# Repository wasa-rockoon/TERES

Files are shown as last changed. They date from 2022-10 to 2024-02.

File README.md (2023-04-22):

# Tiny & Extendable Rocket Electronics Stack

モデルロケットに搭載可能な，小型かつ拡張可能な電装

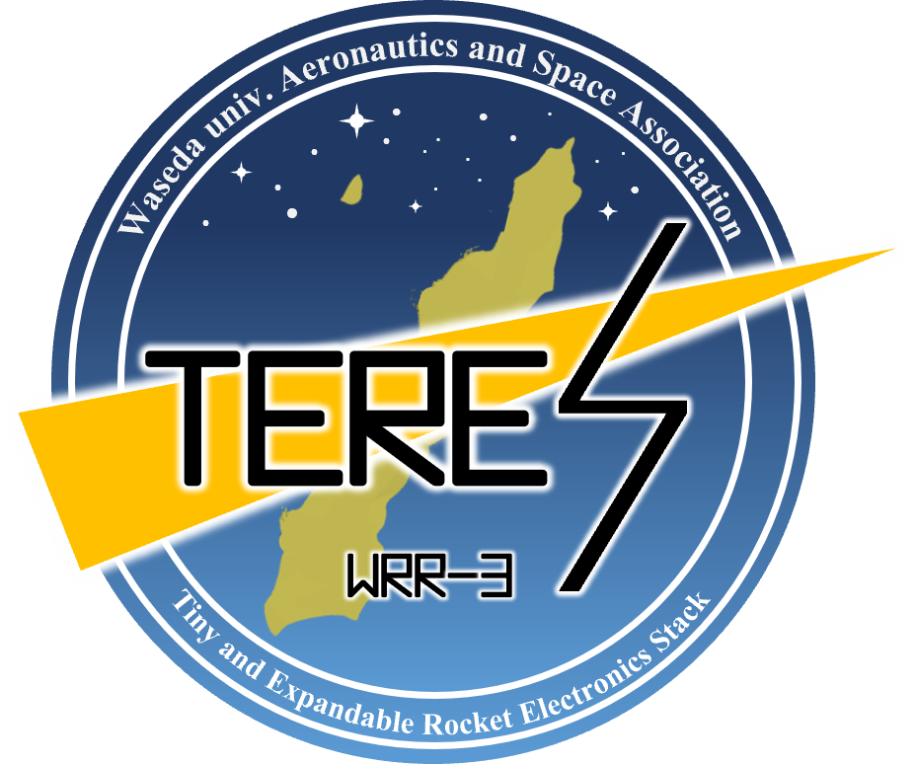
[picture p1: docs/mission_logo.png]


[テレメトリ・コマンド運用](https://wasa-rockoon.github.io/TERES/)

# 要求

- 内径40mmのボディに収まること
- 水密を確保できること
- ミッションや開発状況に応じて組み替え・拡張可能であること

# 仕様

- モジュール式
- マイコン：主にRP2040

## 外形

各モジュールは円盤状で，これを積み重ねて固定した上でロケットのボディ部またはノーズ部に搭載できる．

- 基板外径：36mm
- 基板間コネクタ：2.54mmピッチ ピンヘッダ・ピンソケット
- 固定：M2プラスチックスペーサーx4

## バス

上下のモジュールとUARTで通信し，デイジーチェーンで全体にわたるバスを形成する．

1. GND
2. UART TX
3. V+ (3.6V ~ 6V)
4. UART RX
5. GND

[通信プロトコル](https://github.com/wasa-rockoon/WCCP)

## モジュール

### LiPo電源

- 電源スイッチ
- 外部電源入力
- LiPo充電コントローラ
- LiPo温度センサ
- LiPoヒータ
- ハイサイド電流センサ

### GNSS

- GNSS受信モジュール
- バックアップ用充電池

### センサー

- 9軸センサ
- 気圧センサ
- 外部温度センサ

### テレメトリ

- TWELITE (2.4GHz)
- LoRaモジュール (920MHz)

### ロガー

- MicroSDカード
- Flash
- RTC
- バックアップ用充電池

### カメラ

- ESP32
- カメラモジュール
- マイク

## 詳細設定

### テレメトリ項目・サンプリングコード

1. ダウンリンク(10 Hz)
- GNSS
- LiPo電池残量・温度
- 気圧データ
- 9軸センサの値(姿勢を可視化するプログラムを作れたら)

2. SDカード
- 外部温度センサ(10 Hz)
- 9軸センサの値(姿勢を可視化するプログラムを作れなかったら)(10 Hz)
- カメラ映像
- マイク

### 動作モード

1. 待機フェーズ(重力加速度のみ)
2. 上昇フェーズ(垂直方向加速度>0になってから規定時間 or 気圧低下中)
3. 下降フェーズ(発射から規定時間経過後 or 気圧上昇中)
- パラシュート展開成功(垂直方向加速度==0)
- 弾道落下(ABS(垂直方向加速度)==10)
4. 着陸後フェーズ(気圧変動なし & ABS(加速度ベクトル)==10)

# ビルド

## Arduino

Arduino のライブラリディレクトリに，`software/Library/`のシンボリックリンク（またはコピー）を追加する．

# 使い方
## 動画を生成する
```
python script/make_movie.py "<連番画像フォルダのパス>"
```

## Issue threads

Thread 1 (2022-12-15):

回路設計・基板設計

fujiy, 2022-12-15:
回路設計（配線）

- [x] communication
- [x] gnss
- [x] sensor

基板設計

- [x] communication
- [x] gnss
- [x] logger
- [x] sensor

fujiy, 2022-12-15:
@KeisukeSuganuma
LoRaモジュールとの通信はI2CじゃなくてUARTかな

KeisukeSuganuma, 2022-12-15:
すみません、データシートの読み込みが甘かったです。修正後、GNSSの不足分を足したものと同時にコミットします。

Closed 2023-02-04.

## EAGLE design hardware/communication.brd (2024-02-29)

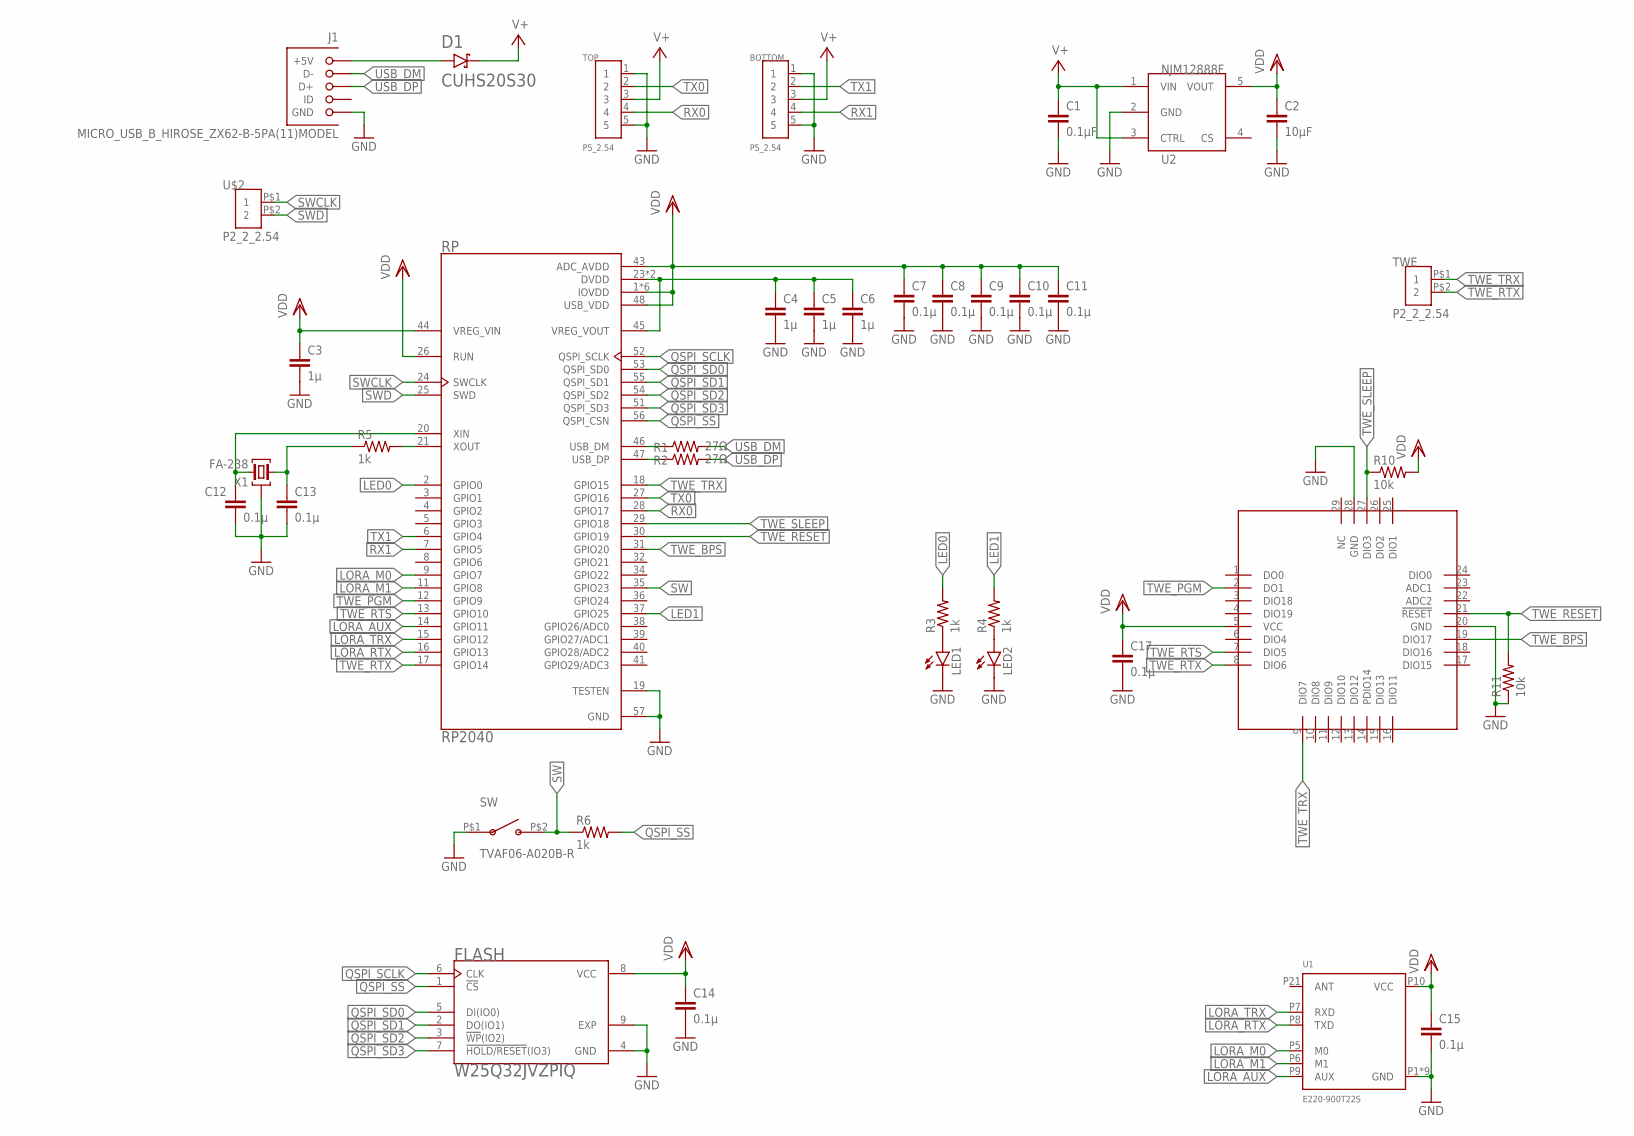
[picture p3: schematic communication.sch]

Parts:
BOTTOM: P5_2.54
C1: 0.1µF; C0402
C2: 10µF; C0402
C3, C4: 1µ; C0402
C5, C6: 1μ; C0402
C7, C8, C9, C10, C11, C15, C17: 0.1µ; C0402
C12, C13, C14: 0.1μ; C0402
D1: CUHS20S30
FLASH: W25Q32JVZPIQ; SON127P600X500X80-9N
J1: MICRO_USB_B_HIROSE_ZX62-B-5PA(11)MODEL; GHI-CONNECTORS_10118192-0001LF(MICRO-USB-B-AMPHENOL-FCI)
LED1, LED2: LEDCHIPLED_0603; CHIPLED_0603
R1, R2: 27Ω; R0402
R3, R4, R5, R6: 1k; R0402
R10, R11: 10k; R0402
RP: RP2040; QFN40P700X700X90-57N
SW: TVAF06-A020B-R
TOP: P5_2.54
TWE: P2_2_2.54; P2_2.54
U1: E220-900T22S
U2: NJM12888F; SOT95P240X110-5N
U$1: LITE
U$2: P2_2_2.54; P2_2.54
X1: FA-238

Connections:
1V2: C4.1, C5.1, C6.1, RP.23 (DVDD), RP.45 (VREG_VOUT), RP.50 (DVDD)
GND: BOTTOM.1, BOTTOM.5, C1.2, C2.2, C3.2, C4.2, C5.2, C6.2, C7.2, C8.2, C9.2, C10.2, C11.2, C12.2, C13.2, C14.2, C15.2, C17.2, FLASH.4 (GND), FLASH.9 (EXP), J1.CGND1 (GND), J1.CGND2 (GND), J1.CGND3 (GND), J1.CGND4 (GND), J1.CGND5 (GND), J1.CGND6 (GND), J1.GND, LED1.C, LED2.C, R11.1, RP.19 (TESTEN), RP.57 (GND), SW.P$1 (A), TOP.1, TOP.5, U1.P1 (GND), U1.P2 (GND), U1.P3 (GND), U1.P4 (GND), U1.P11 (GND), U1.P13 (GND), U1.P19 (GND), U1.P20 (GND), U1.P22 (GND), U2.2 (GND), U$1.20 (GND), U$1.28 (GND), X1.2 (G), X1.4 (G)
LED0: R3.2, RP.2 (GPIO0)
LED1: R4.2, RP.37 (GPIO25)
LORA_AUX: RP.14 (GPIO11), U1.P9 (AUX)
LORA_M0: RP.9 (GPIO7), U1.P5 (M0)
LORA_M1: RP.11 (GPIO8), U1.P6 (M1)
LORA_RTX: RP.16 (GPIO13), U1.P8 (TXD)
LORA_TRX: RP.15 (GPIO12), U1.P7 (RXD)
unnamed: D1.A, J1.VBUS (+5V)
unnamed: LED1.A, R3.1
unnamed: LED2.A, R4.1
unnamed: C13.1, R5.1, X1.1
QSPI_SCLK: FLASH.6 (CLK), RP.52 (QSPI_SCLK)
QSPI_SD0: FLASH.5 (DI(IO0)), RP.53 (QSPI_SD0)
QSPI_SD1: FLASH.2 (DO(IO1)), RP.55 (QSPI_SD1)
QSPI_SD2: FLASH.3 (!WP!(IO2)), RP.54 (QSPI_SD2)
QSPI_SD3: FLASH.7 (!HOLD/RESET!(IO3)), RP.51 (QSPI_SD3)
QSPI_SS: FLASH.1 (!CS), R6.2, RP.56 (QSPI_CSN)
RX0: RP.28 (GPIO17), TOP.4
RX1: BOTTOM.4, RP.7 (GPIO5)
SW: R6.1, RP.35 (GPIO23), SW.P$2 (B)
SWCLK: RP.24 (SWCLK), U$2.P$1 (1)
SWD: RP.25 (SWD), U$2.P$2 (2)
TWE_BPS: RP.31 (GPIO20), U$1.19 (DIO17)
TWE_PGM: RP.12 (GPIO9), U$1.2 (DO1)
TWE_RESET: R11.2, RP.30 (GPIO19), U$1.21 (!RESET!)
TWE_RTS: RP.13 (GPIO10), U$1.7 (DIO5)
TWE_RTX: RP.17 (GPIO14), TWE.P$2 (2), U$1.8 (DIO6)
TWE_SLEEP: R10.1, RP.29 (GPIO18), U$1.27 (DIO3)
TWE_TRX: RP.18 (GPIO15), TWE.P$1 (1), U$1.9 (DIO7)
TX0: RP.27 (GPIO16), TOP.2
TX1: BOTTOM.2, RP.6 (GPIO4)
USB_DM: J1.D-, R1.2
USB_DM_1: R1.1, RP.46 (USB_DM)
USB_DP: J1.D+, R2.2
USB_DP_1: R2.1, RP.47 (USB_DP)
V+: BOTTOM.3, C1.1, D1.C, TOP.3, U2.1 (VIN), U2.3 (CTRL)
VDD: C2.1, C3.1, C7.1, C8.1, C9.1, C10.1, C11.1, C14.1, C15.1, C17.1, FLASH.8 (VCC), R10.2, RP.1 (IOVDD), RP.10 (IOVDD), RP.22 (IOVDD), RP.26 (RUN), RP.33 (IOVDD), RP.42 (IOVDD), RP.43 (ADC_AVDD), RP.44 (VREG_VIN), RP.48 (USB_VDD), RP.49 (IOVDD), U1.P10 (VCC), U2.5 (VOUT), U$1.5 (VCC)
XIN1: C12.1, RP.20 (XIN), X1.3 (2)
XOUT1: R5.2, RP.21 (XOUT)

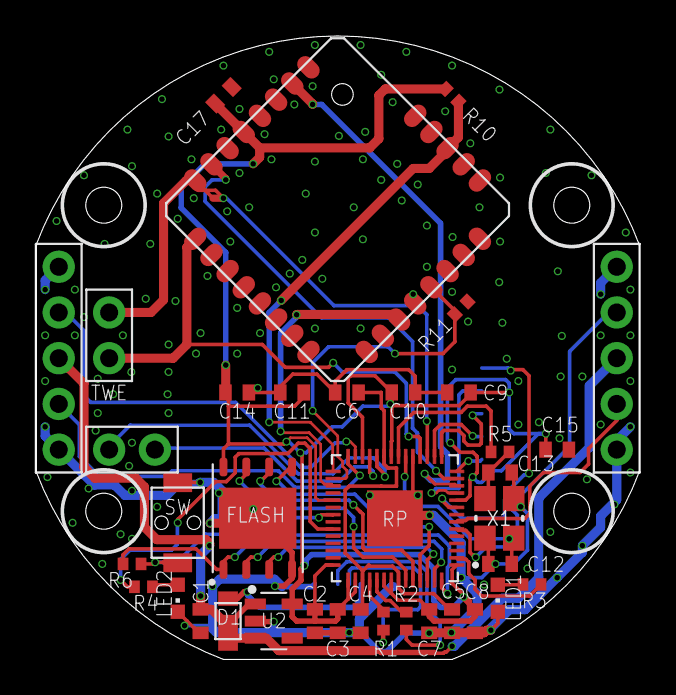
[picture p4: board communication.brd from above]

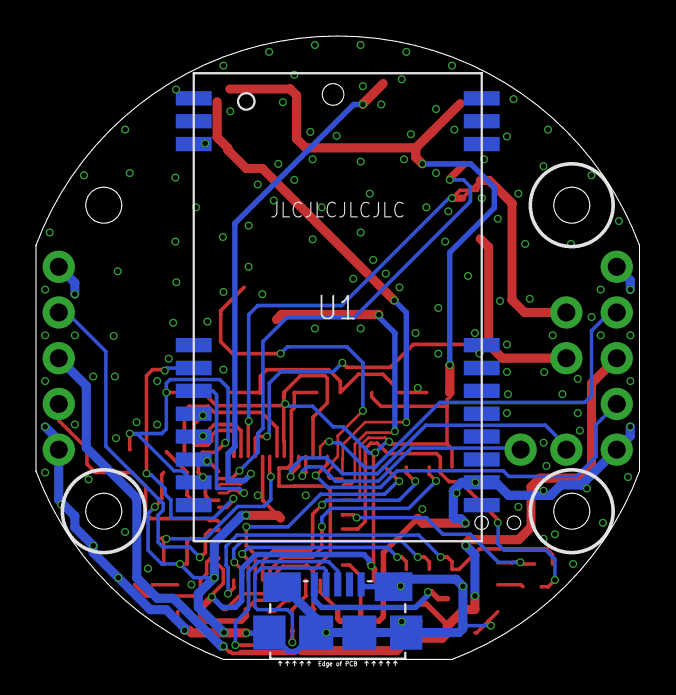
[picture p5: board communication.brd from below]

Board: 2 copper layers, 33.5 x 34.6 mm, 39 parts (2 on the bottom side), 41 nets.

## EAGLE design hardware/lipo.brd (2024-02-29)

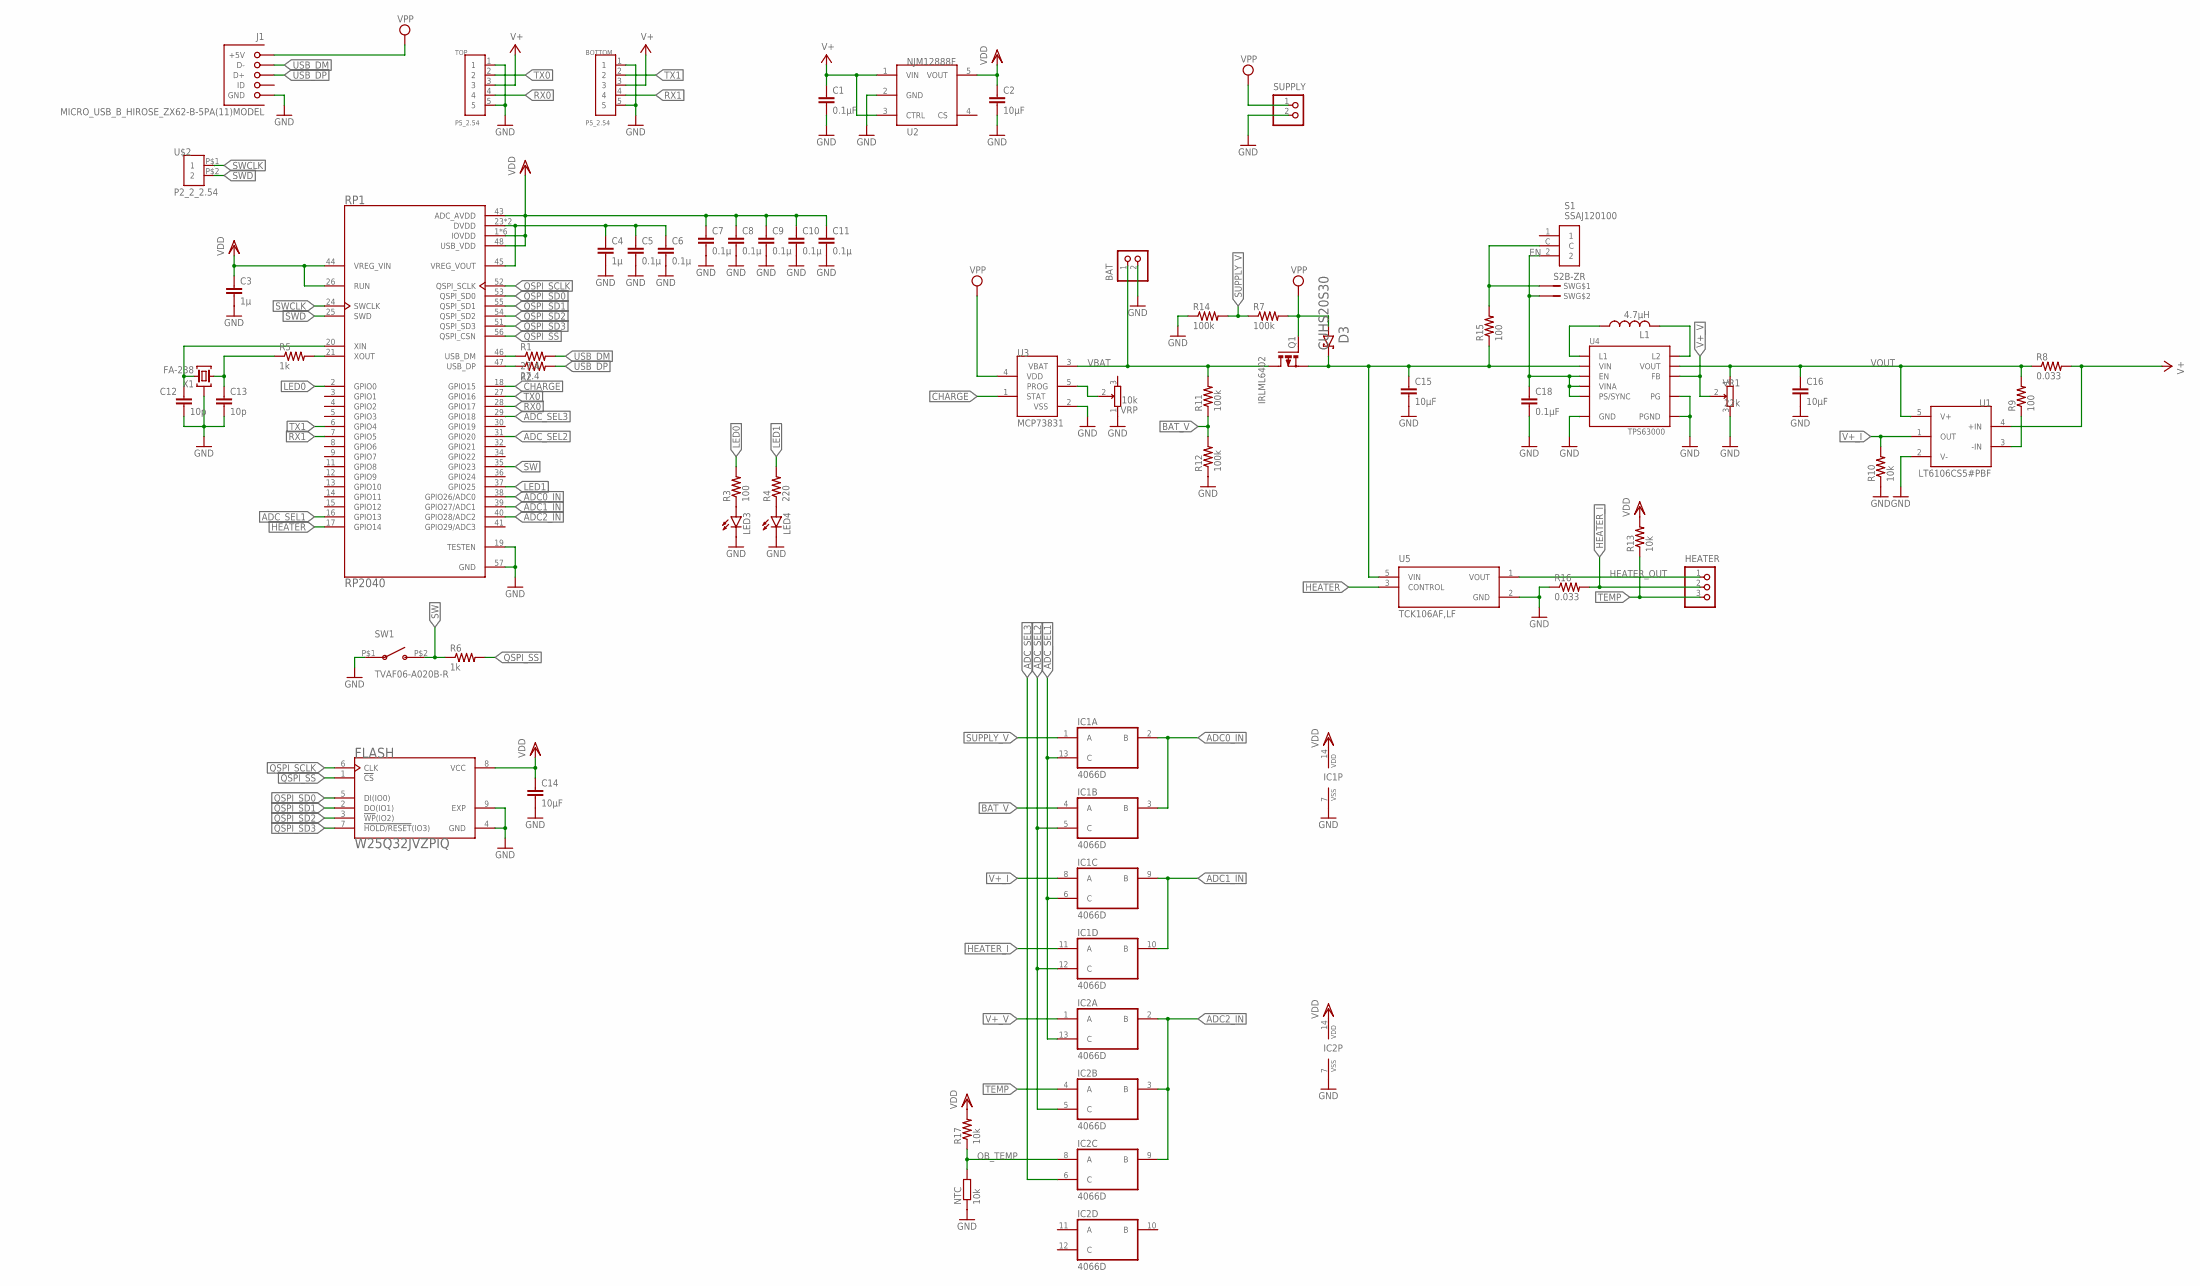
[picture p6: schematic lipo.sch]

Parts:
BAT: S2B-PH-K-S
BOTTOM: P5_2.54
C1, C18: 0.1µF; C0402
C2, C14, C15, C16: 10µF; C0402
C3, C4: 1µ; C0402
C5, C6, C7, C8, C9, C10, C11: 0.1µ; C0402
C12, C13: 10p; C0402
D3: CUHS20S30
FLASH: W25Q32JVZPIQ; SON127P600X500X80-9N
HEATER: S3B-PH-K-S
IC1, IC2: 4066D; SO14
J1: MICRO_USB_B_HIROSE_ZX62-B-5PA(11)MODEL; GHI-CONNECTORS_10118192-0001LF(MICRO-USB-B-AMPHENOL-FCI)
L1: 4.7µH; L3225M
LED3, LED4: LEDCHIPLED_0603; CHIPLED_0603
NTC: 10k; R0603
Q1: IRLML6402; SOT-23
R1, R2: 27.4; R0402
R3, R9, R15: 100; R0402
R4: 220; R0402
R5, R6: 1k; R0402
R7, R11, R12, R14: 100k; R0402
R8, R16: 0.033; R0603
R10, R13, R17: 10k; R0402
RP1: RP2040; QFN40P700X700X90-57N
S1: SSAJ120100
SUPPLY: S2B-PH-K-S
SW: S2B-ZR
SW1: TVAF06-A020B-R
TOP: P5_2.54
U1: LT6106CS5#PBF; SOT95P280X100-5N_LT6106CS5#PBF
U2: NJM12888F; SOT95P240X110-5N
U3: MCP73831; SOT23-5L
U4: TPS63000; 10-VFDFN
U5: TCK106AF,LF; IC_TCK106AF,LF
U$2: P2_2_2.54; P2_2.54
VR1: 22k; PVZ3A
VRP: 10k; PVZ3A
X1: FA-238

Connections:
1V2: C4.1, C5.1, C6.1, RP1.23 (DVDD), RP1.45 (VREG_VOUT), RP1.50 (DVDD)
ADC0_IN: IC1.2 (B), IC1.3 (B), RP1.38 (GPIO26/ADC0)
ADC1_IN: IC1.9 (B), IC1.10 (B), RP1.39 (GPIO27/ADC1)
ADC2_IN: IC2.2 (B), IC2.3 (B), IC2.9 (B), RP1.40 (GPIO28/ADC2)
ADC_SEL1: IC1.6 (C), IC1.13 (C), IC2.13 (C), RP1.16 (GPIO13)
ADC_SEL2: IC1.5 (C), IC1.12 (C), IC2.5 (C), RP1.31 (GPIO20)
ADC_SEL3: IC2.6 (C), RP1.29 (GPIO18)
BAT_V: IC1.4 (A), R11.1, R12.2
CHARGE: RP1.18 (GPIO15), U3.1 (STAT)
EN: C18.1, S1.2, SW.2, U4.6 (EN), U4.7 (PS/SYNC), U4.8 (VINA)
GND: BAT.2, BOTTOM.1, BOTTOM.5, C1.2, C2.2, C3.2, C4.2, C5.2, C6.2, C7.2, C8.2, C9.2, C10.2, C11.2, C12.2, C13.2, C14.2, C15.2, C16.2, C18.2, FLASH.4 (GND), FLASH.9 (EXP), IC1.7 (VSS), IC2.7 (VSS), J1.CGND1 (GND), J1.CGND2 (GND), J1.CGND3 (GND), J1.CGND4 (GND), J1.CGND5 (GND), J1.CGND6 (GND), J1.GND, LED3.C, LED4.C, NTC.1, R10.1, R12.1, R14.1, R16.1, RP1.19 (TESTEN), RP1.57 (GND), SUPPLY.2, SW1.P$1 (A), TOP.1, TOP.5, U1.2 (V-), U2.2 (GND), U3.2 (VSS), U4.3 (PGND), U4.9 (GND), U4.P$1 (PG), U4.P$2 (PG), U4.P$3 (PG), U4.P$4 (PG), U4.P$5 (PG), U5.2 (GND), VR1.3, VRP.1, X1.2 (G), X1.4 (G)
HEATER: RP1.17 (GPIO14), U5.3 (CONTROL)
HEATER_I: HEATER.2, IC1.11 (A), R16.2
HEATER_OUT: HEATER.1, U5.1 (VOUT)
LED0: R3.2, RP1.2 (GPIO0)
LED1: R4.2, RP1.37 (GPIO25)
unnamed: L1.1, U4.4 (L1)
unnamed: R9.1, U1.3 (-IN)
unnamed: U3.5 (PROG), VRP.2
unnamed: L1.2, U4.2 (L2)
unnamed: LED3.A, R3.1
unnamed: LED4.A, R4.1
unnamed: C13.1, R5.1, X1.1
unnamed: R15.2, S1.C, SW.1
OB_TEMP: IC2.8 (A), NTC.2, R17.1
QSPI_SCLK: FLASH.6 (CLK), RP1.52 (QSPI_SCLK)
QSPI_SD0: FLASH.5 (DI(IO0)), RP1.53 (QSPI_SD0)
QSPI_SD1: FLASH.2 (DO(IO1)), RP1.55 (QSPI_SD1)
QSPI_SD2: FLASH.3 (!WP!(IO2)), RP1.54 (QSPI_SD2)
QSPI_SD3: FLASH.7 (!HOLD/RESET!(IO3)), RP1.51 (QSPI_SD3)
QSPI_SS: FLASH.1 (!CS), R6.2, RP1.56 (QSPI_CSN)
RX0: RP1.28 (GPIO17), TOP.4
RX1: BOTTOM.4, RP1.7 (GPIO5)
SUPPLY_V: IC1.1 (A), R7.1, R14.2
SW: R6.1, RP1.35 (GPIO23), SW1.P$2 (B)
SWCLK: RP1.24 (SWCLK), U$2.P$1 (1)
SWD: RP1.25 (SWD), U$2.P$2 (2)
TEMP: HEATER.3, IC2.4 (A), R13.1
TX0: RP1.27 (GPIO16), TOP.2
TX1: BOTTOM.2, RP1.6 (GPIO4)
USB_DM: J1.D-, R1.2
USB_DM_1: R1.1, RP1.46 (USB_DM)
USB_DP: J1.D+, R2.2
USB_DP_1: R2.1, RP1.47 (USB_DP)
V+: BOTTOM.3, C1.1, R8.2, TOP.3, U1.4 (+IN), U2.1 (VIN), U2.3 (CTRL)
V+_I: IC1.8 (A), R10.2, U1.1 (OUT)
V+_V: IC2.1 (A), U4.10 (FB), VR1.2
VBAT: BAT.1, Q1.P3 (D), R11.2, U3.3 (VBAT)
VBAT_: C15.1, D3.C, Q1.P2 (S), R15.1, U4.5 (VIN), U5.5 (VIN)
VDD: C2.1, C3.1, C7.1, C8.1, C9.1, C10.1, C11.1, C14.1, FLASH.8 (VCC), IC1.14 (VDD), IC2.14 (VDD), R13.2, R17.2, RP1.1 (IOVDD), RP1.10 (IOVDD), RP1.22 (IOVDD), RP1.26 (RUN), RP1.33 (IOVDD), RP1.42 (IOVDD), RP1.43 (ADC_AVDD), RP1.44 (VREG_VIN), RP1.48 (USB_VDD), RP1.49 (IOVDD), U2.5 (VOUT)
VOUT: C16.1, R8.1, R9.2, U1.5 (V+), U4.1 (VOUT), VR1.1
VPP: D3.A, J1.VBUS (+5V), Q1.P1 (G), R7.2, SUPPLY.1, U3.4 (VDD)
XIN1: C12.1, RP1.20 (XIN), X1.3 (2)
XOUT1: R5.2, RP1.21 (XOUT)

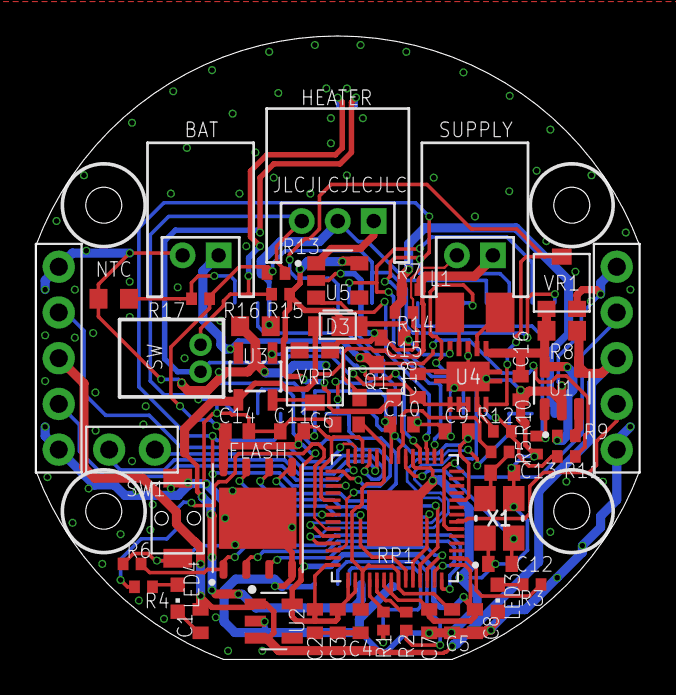
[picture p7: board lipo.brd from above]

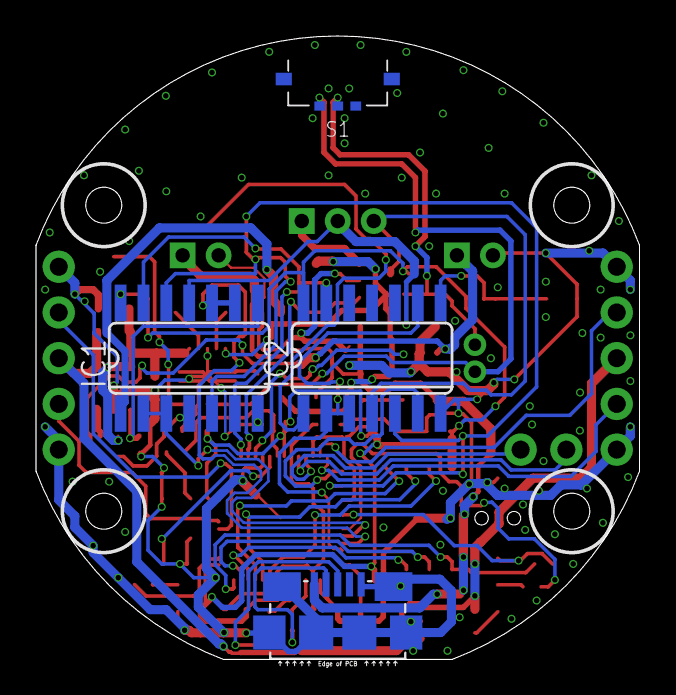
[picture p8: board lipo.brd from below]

Board: 2 copper layers, 33.5 x 34.6 mm, 62 parts (4 on the bottom side), 54 nets.

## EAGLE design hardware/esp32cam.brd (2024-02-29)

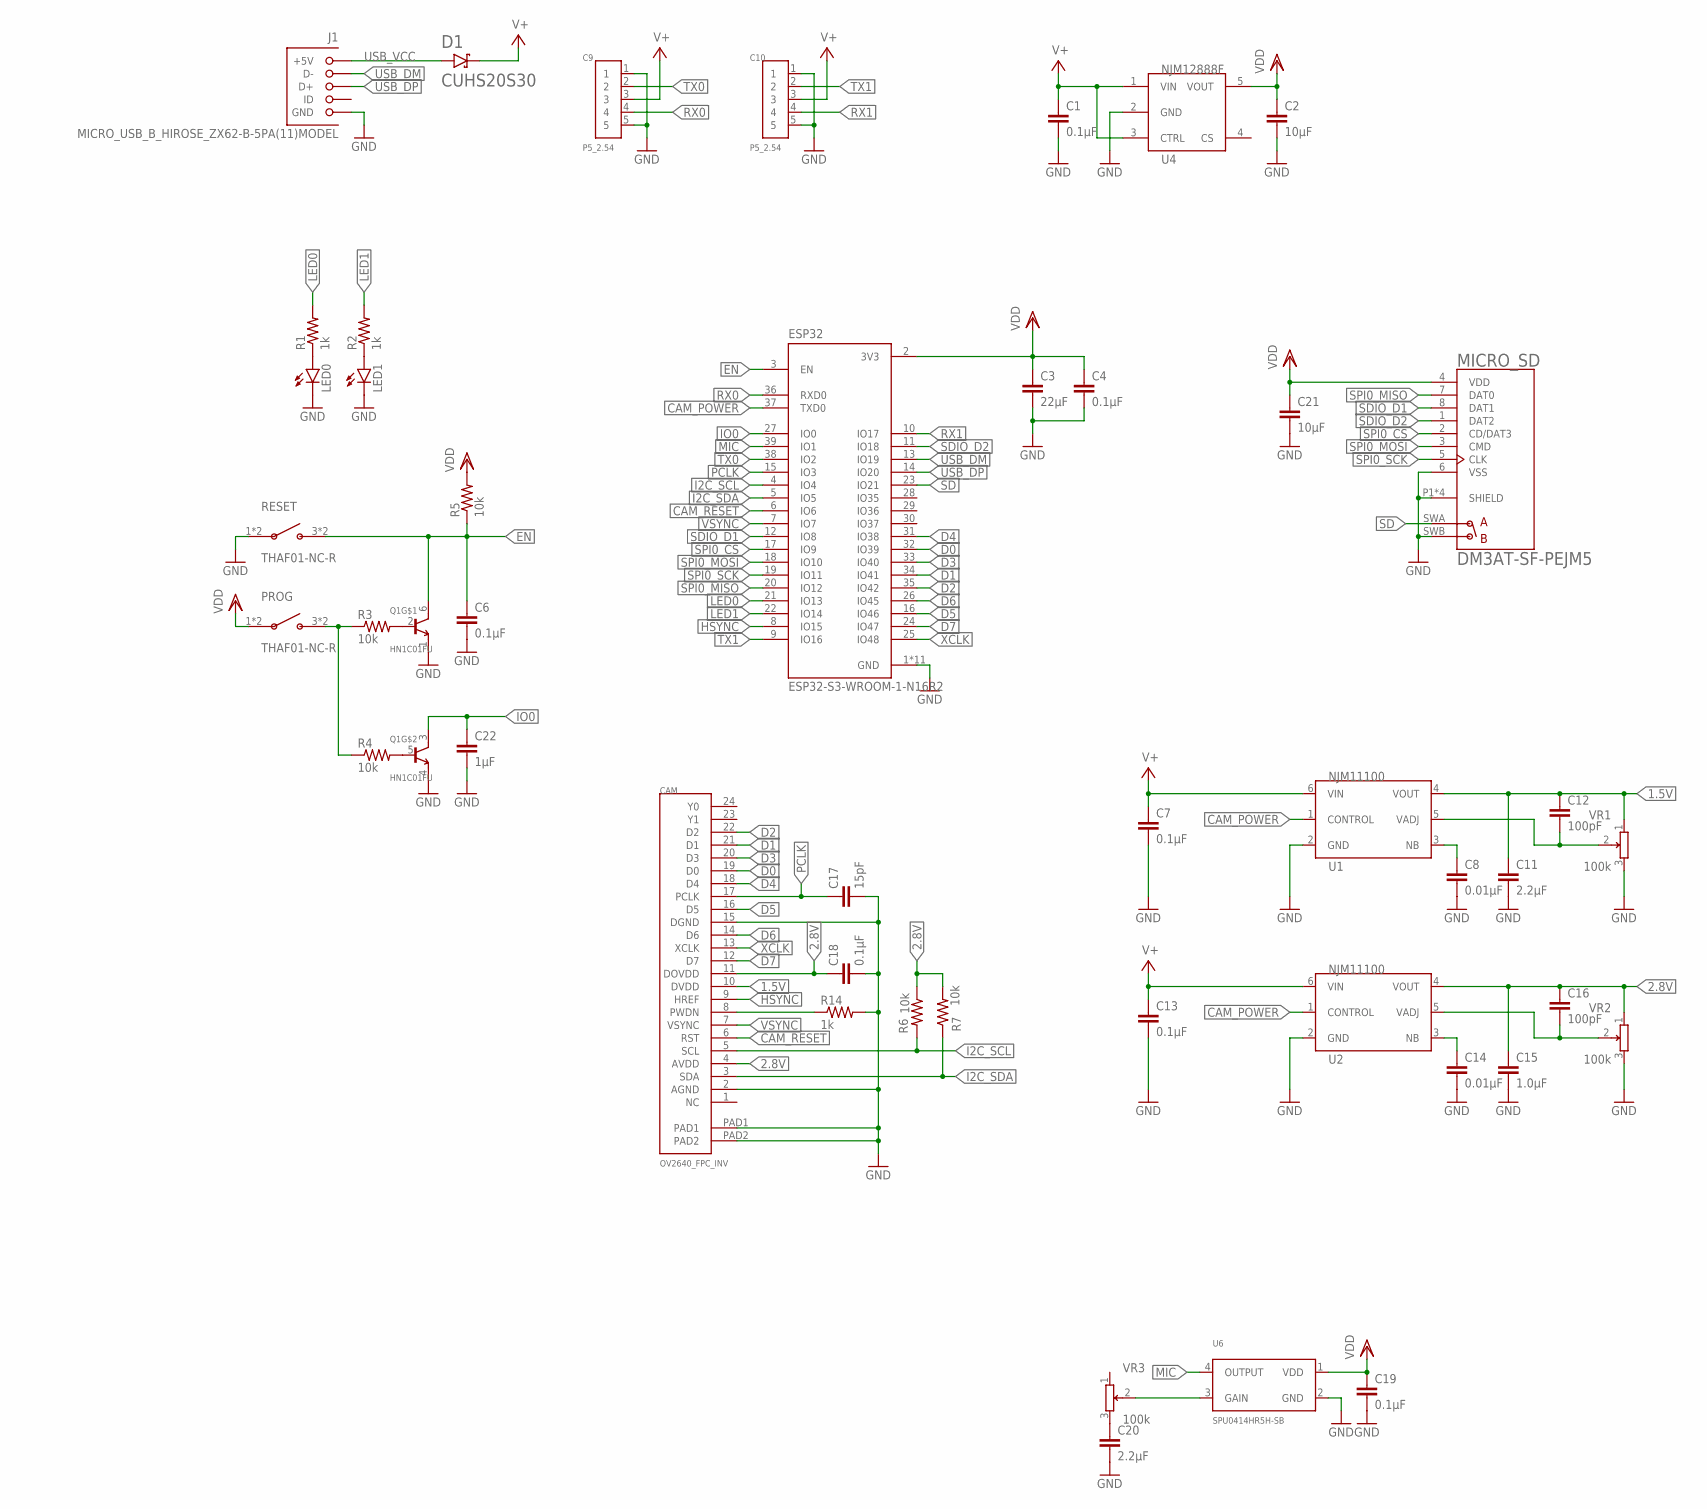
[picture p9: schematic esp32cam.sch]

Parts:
C1, C4, C6, C7, C13, C18, C19: 0.1µF; C0402
C2, C21: 10µF; C0402
C3: 22µF; C0402
C8, C14: 0.01µF; C0402
C9, C10: P5_2.54
C11, C20: 2.2µF; C0402
C12, C16: 100pF; C0402
C15: 1.0µF; C0402
C17: 15pF; C0402
C22: 1µF; C0402
CAM: OV2640_FPC_INV; FH12-24S-0.5SH
D1: CUHS20S30
ESP32: ESP32-S3-WROOM-1-N16R2; XCVR_ESP32-S3-WROOM-1-N16R2
J1: MICRO_USB_B_HIROSE_ZX62-B-5PA(11)MODEL; GHI-CONNECTORS_10118192-0001LF(MICRO-USB-B-AMPHENOL-FCI)
LED0, LED1: LEDCHIPLED_0603; CHIPLED_0603
MICRO_SD: DM3AT-SF-PEJM5; HRS_DM3AT-SF-PEJM5
PROG: THAF01-NC-R
Q1: HN1C01FU; SOT-363
R1, R2, R14: 1k; R0402
R3, R4, R5, R6, R7: 10k; R0402
RESET: THAF01-NC-R
U1, U2: NJM11100; SOT95P240X110-6N
U4: NJM12888F; SOT95P240X110-5N
U6: SPU0414HR5H-SB
VR1, VR2, VR3: 100k; PVZ3A

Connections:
1.5V: C11.1, C12.1, CAM.10 (DVDD), U1.4 (VOUT), VR1.1
2.8V: C15.1, C16.1, C18.1, CAM.4 (AVDD), CAM.11 (DOVDD), R6.1, R7.2, U2.4 (VOUT), VR2.1
CAM_POWER: ESP32.37 (TXD0), U1.1 (CONTROL), U2.1 (CONTROL)
CAM_RESET: CAM.6 (RST), ESP32.6 (IO6)
D0: CAM.19 (D0), ESP32.32 (IO39)
D1: CAM.21 (D1), ESP32.34 (IO41)
D2: CAM.22 (D2), ESP32.35 (IO42)
D3: CAM.20 (D3), ESP32.33 (IO40)
D4: CAM.18 (D4), ESP32.31 (IO38)
D5: CAM.16 (D5), ESP32.16 (IO46)
D6: CAM.14 (D6), ESP32.26 (IO45)
D7: CAM.12 (D7), ESP32.24 (IO47)
EN: C6.1, ESP32.3 (EN), Q1.6 (C), R5.1, RESET.3 (B), RESET.4 (B)
GND: C1.2, C2.2, C3.2, C4.2, C6.2, C7.2, C8.2, C9.1, C9.5, C10.1, C10.5, C11.2, C13.2, C14.2, C15.2, C17.2, C18.2, C19.2, C20.2, C21.2, C22.2, CAM.2 (AGND), CAM.15 (DGND), CAM.PAD1, CAM.PAD2, ESP32.1 (GND), ESP32.40 (GND), ESP32.41_1 (GND), ESP32.41_2 (GND), ESP32.41_3 (GND), ESP32.41_4 (GND), ESP32.41_5 (GND), ESP32.41_6 (GND), ESP32.41_7 (GND), ESP32.41_8 (GND), ESP32.41_9 (GND), J1.CGND1 (GND), J1.CGND2 (GND), J1.CGND3 (GND), J1.CGND4 (GND), J1.CGND5 (GND), J1.CGND6 (GND), J1.GND, LED0.C, LED1.C, MICRO_SD.6 (VSS), MICRO_SD.P1 (SHIELD), MICRO_SD.P2 (SHIELD), MICRO_SD.P3 (SHIELD), MICRO_SD.P4 (SHIELD), MICRO_SD.SWB (B), Q1.1 (E), Q1.4 (E), R14.2, RESET.1 (A), RESET.2 (A), U1.2 (GND), U2.2 (GND), U4.2 (GND), U6.2 (GND), VR1.3, VR2.3
HSYNC: CAM.9 (HREF), ESP32.8 (IO15)
I2C_SCL: CAM.5 (SCL), ESP32.4 (IO4), R6.2
I2C_SDA: CAM.3 (SDA), ESP32.5 (IO5), R7.1
IO0: C22.1, ESP32.27 (IO0), Q1.3 (C)
LED0: ESP32.21 (IO13), R1.2
LED1: ESP32.22 (IO14), R2.2
MIC: ESP32.39 (IO1), U6.4 (OUTPUT)
unnamed: C8.1, U1.3 (NB)
unnamed: C12.2, U1.5 (VADJ), VR1.2
unnamed: C14.1, U2.3 (NB)
unnamed: C16.2, U2.5 (VADJ), VR2.2
unnamed: PROG.3 (B), PROG.4 (B), R3.1, R4.1
unnamed: LED0.A, R1.1
unnamed: LED1.A, R2.1
unnamed: Q1.2 (B), R3.2
unnamed: CAM.8 (PWDN), R14.1
unnamed: Q1.5 (B), R4.2
unnamed: U6.3 (GAIN), VR3.2
unnamed: C20.1, VR3.3
PCLK: C17.1, CAM.17 (PCLK), ESP32.15 (IO3)
RX0: C9.4, ESP32.36 (RXD0)
RX1: C10.4, ESP32.10 (IO17)
SD: ESP32.23 (IO21), MICRO_SD.SWA (A)
SDIO_D1: ESP32.12 (IO8), MICRO_SD.8 (DAT1)
SDIO_D2: ESP32.11 (IO18), MICRO_SD.1 (DAT2)
SPI0_CS: ESP32.17 (IO9), MICRO_SD.2 (CD/DAT3)
SPI0_MISO: ESP32.20 (IO12), MICRO_SD.7 (DAT0)
SPI0_MOSI: ESP32.18 (IO10), MICRO_SD.3 (CMD)
SPI0_SCK: ESP32.19 (IO11), MICRO_SD.5 (CLK)
TX0: C9.2, ESP32.38 (IO2)
TX1: C10.2, ESP32.9 (IO16)
USB_DM: ESP32.13 (IO19), J1.D-
USB_DP: ESP32.14 (IO20), J1.D+
USB_VCC: D1.A, J1.VBUS (+5V)
V+: C1.1, C7.1, C9.3, C10.3, C13.1, D1.C, U1.6 (VIN), U2.6 (VIN), U4.1 (VIN), U4.3 (CTRL)
VDD: C2.1, C3.1, C4.1, C19.1, C21.1, ESP32.2 (3V3), MICRO_SD.4 (VDD), PROG.1 (A), PROG.2 (A), R5.2, U4.5 (VOUT), U6.1 (VDD)
VSYNC: CAM.7 (VSYNC), ESP32.7 (IO7)
XCLK: CAM.13 (XCLK), ESP32.25 (IO48)

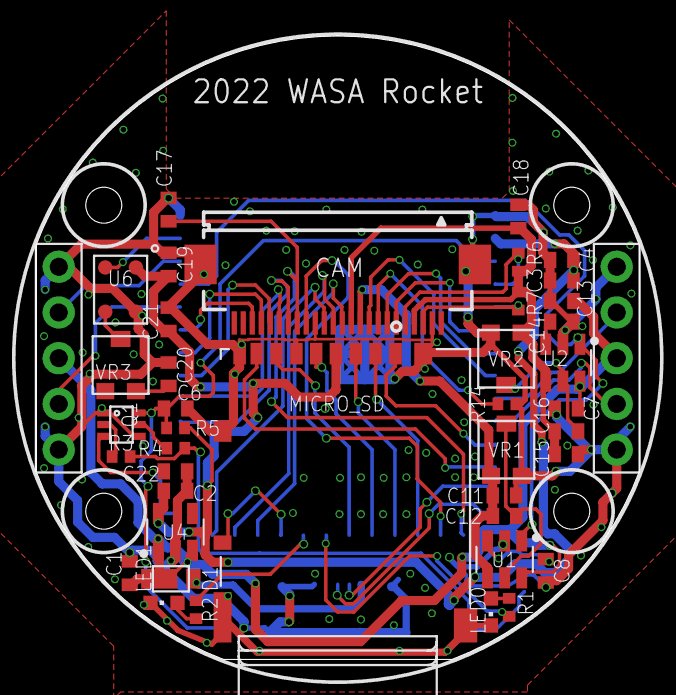
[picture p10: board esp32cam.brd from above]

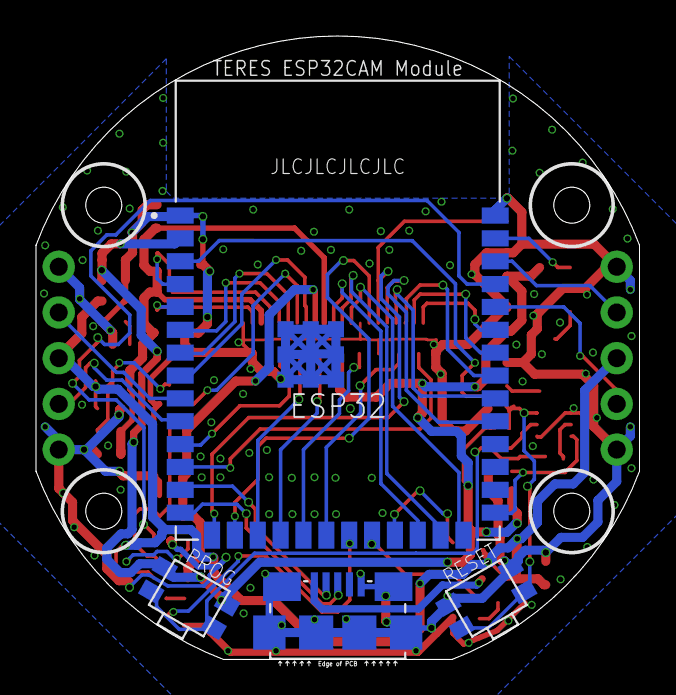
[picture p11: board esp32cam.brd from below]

Board: 2 copper layers, 33.5 x 34.6 mm, 46 parts (4 on the bottom side), 52 nets.

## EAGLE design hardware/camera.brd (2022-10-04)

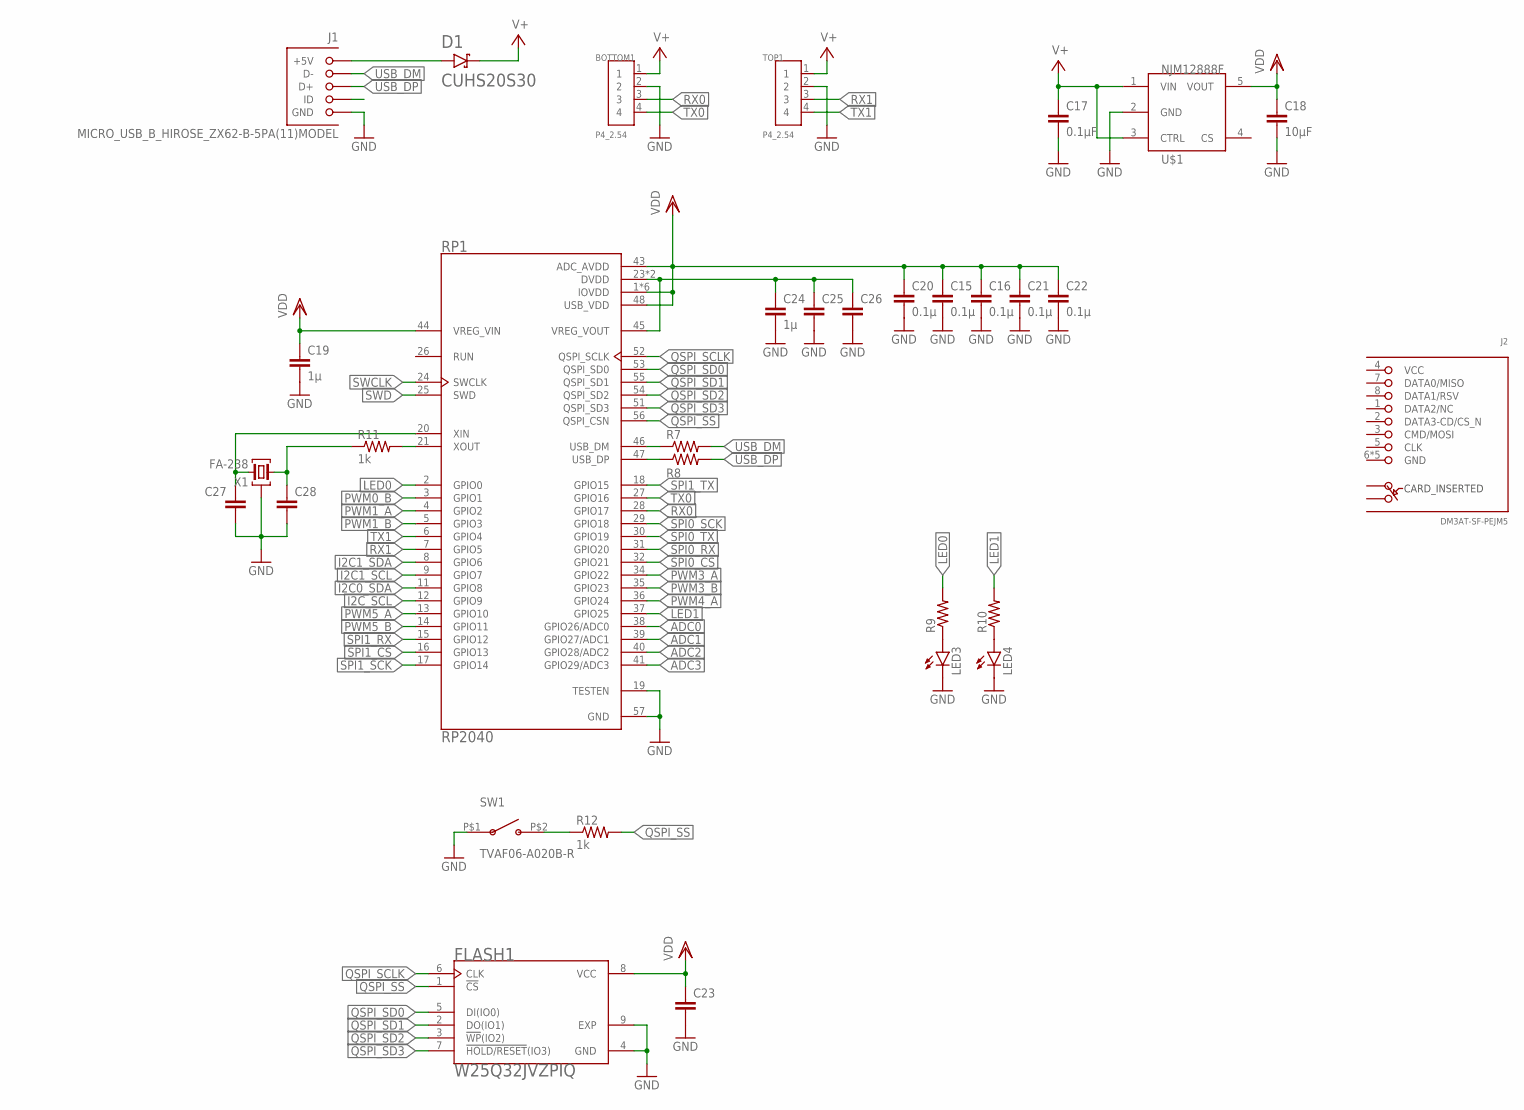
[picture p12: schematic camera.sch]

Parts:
BOTTOM1: P4_2.54
C15, C16, C20, C21, C22: 0.1µ; C0402
C17: 0.1µF; C0402
C18: 10µF; C0402
C19, C24: 1µ; C0402
C23, C25, C26, C27, C28: C-EUC0402; C0402
D1: CUHS20S30
FLASH1: W25Q32JVZPIQ; SON127P600X500X80-9N
J1: MICRO_USB_B_HIROSE_ZX62-B-5PA(11)MODEL; GHI-CONNECTORS_10118192-0001LF(MICRO-USB-B-AMPHENOL-FCI)
J2: DM3AT-SF-PEJM5
LED3, LED4: LEDCHIPLED_0603; CHIPLED_0603
R7, R8, R9, R10: R-US_R0402; R0402
R11, R12: 1k; R0402
RP1: RP2040; QFN40P700X700X90-57N
SW1: TVAF06-A020B-R
TOP1: P4_2.54
U$1: NJM12888F; SOT95P240X110-5N
X1: FA-238

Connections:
1V2: C24.1, C25.1, C26.1, RP1.23 (DVDD), RP1.45 (VREG_VOUT), RP1.50 (DVDD)
ADC0: RP1.38 (GPIO26/ADC0)
ADC1: RP1.39 (GPIO27/ADC1)
ADC2: RP1.40 (GPIO28/ADC2)
ADC3: RP1.41 (GPIO29/ADC3)
GND: BOTTOM1.2, C15.2, C16.2, C17.2, C18.2, C19.2, C20.2, C21.2, C22.2, C23.2, C24.2, C25.2, C26.2, C27.2, C28.2, FLASH1.4 (GND), FLASH1.9 (EXP), J1.CGND1 (GND), J1.CGND2 (GND), J1.CGND3 (GND), J1.CGND4 (GND), J1.CGND5 (GND), J1.CGND6 (GND), J1.GND, LED3.C, LED4.C, RP1.19 (TESTEN), RP1.57 (GND), SW1.P$1 (A), TOP1.2, U$1.2 (GND), X1.2 (G), X1.4 (G)
I2C0_SDA: RP1.11 (GPIO8)
I2C1_SCL: RP1.9 (GPIO7)
I2C1_SDA: RP1.8 (GPIO6)
I2C_SCL: RP1.12 (GPIO9)
LED0: R9.2, RP1.2 (GPIO0)
LED1: R10.2, RP1.37 (GPIO25)
unnamed: D1.A, J1.VBUS (+5V)
unnamed: LED3.A, R9.1
unnamed: LED4.A, R10.1
unnamed: C28.1, R11.1, X1.1
unnamed: R12.1, SW1.P$2 (B)
PWM0_B: RP1.3 (GPIO1)
PWM1_A: RP1.4 (GPIO2)
PWM1_B: RP1.5 (GPIO3)
PWM3_A: RP1.34 (GPIO22)
PWM3_B: RP1.35 (GPIO23)
PWM4_A: RP1.36 (GPIO24)
PWM5_A: RP1.13 (GPIO10)
PWM5_B: RP1.14 (GPIO11)
QSPI_SCLK: FLASH1.6 (CLK), RP1.52 (QSPI_SCLK)
QSPI_SD0: FLASH1.5 (DI(IO0)), RP1.53 (QSPI_SD0)
QSPI_SD1: FLASH1.2 (DO(IO1)), RP1.55 (QSPI_SD1)
QSPI_SD2: FLASH1.3 (!WP!(IO2)), RP1.54 (QSPI_SD2)
QSPI_SD3: FLASH1.7 (!HOLD/RESET!(IO3)), RP1.51 (QSPI_SD3)
QSPI_SS: FLASH1.1 (!CS), R12.2, RP1.56 (QSPI_CSN)
RX0: BOTTOM1.3, RP1.28 (GPIO17)
RX1: RP1.7 (GPIO5), TOP1.3
SPI0_CS: RP1.32 (GPIO21)
SPI0_RX: RP1.31 (GPIO20)
SPI0_SCK: RP1.29 (GPIO18)
SPI0_TX: RP1.30 (GPIO19)
SPI1_CS: RP1.16 (GPIO13)
SPI1_RX: RP1.15 (GPIO12)
SPI1_SCK: RP1.17 (GPIO14)
SPI1_TX: RP1.18 (GPIO15)
SWCLK: RP1.24 (SWCLK)
SWD: RP1.25 (SWD)
TX0: BOTTOM1.4, RP1.27 (GPIO16)
TX1: RP1.6 (GPIO4), TOP1.4
USB_DM: J1.D-, R7.2
USB_DM_1: R7.1, RP1.46 (USB_DM)
USB_DP: J1.D+, R8.2
USB_DP_1: R8.1, RP1.47 (USB_DP)
V+: BOTTOM1.1, C17.1, D1.C, TOP1.1, U$1.1 (VIN), U$1.3 (CTRL)
VDD: C15.1, C16.1, C18.1, C19.1, C20.1, C21.1, C22.1, C23.1, FLASH1.8 (VCC), RP1.1 (IOVDD), RP1.10 (IOVDD), RP1.22 (IOVDD), RP1.33 (IOVDD), RP1.42 (IOVDD), RP1.43 (ADC_AVDD), RP1.44 (VREG_VIN), RP1.48 (USB_VDD), RP1.49 (IOVDD), U$1.5 (VOUT)
XIN1: C27.1, RP1.20 (XIN), X1.3 (2)
XOUT1: R11.2, RP1.21 (XOUT)

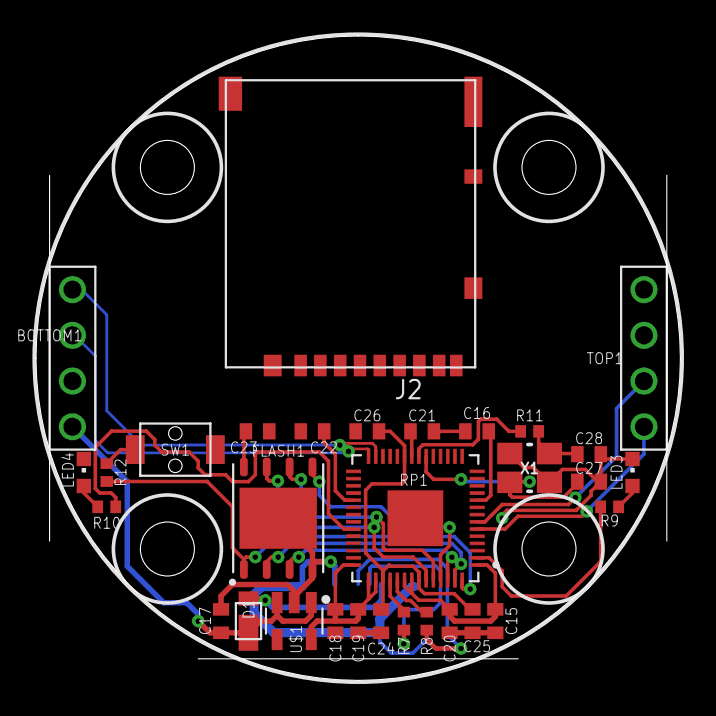
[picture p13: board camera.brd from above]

Board: 2 copper layers, 35.8 x 35.8 mm, 32 parts (1 on the bottom side), 27 nets.

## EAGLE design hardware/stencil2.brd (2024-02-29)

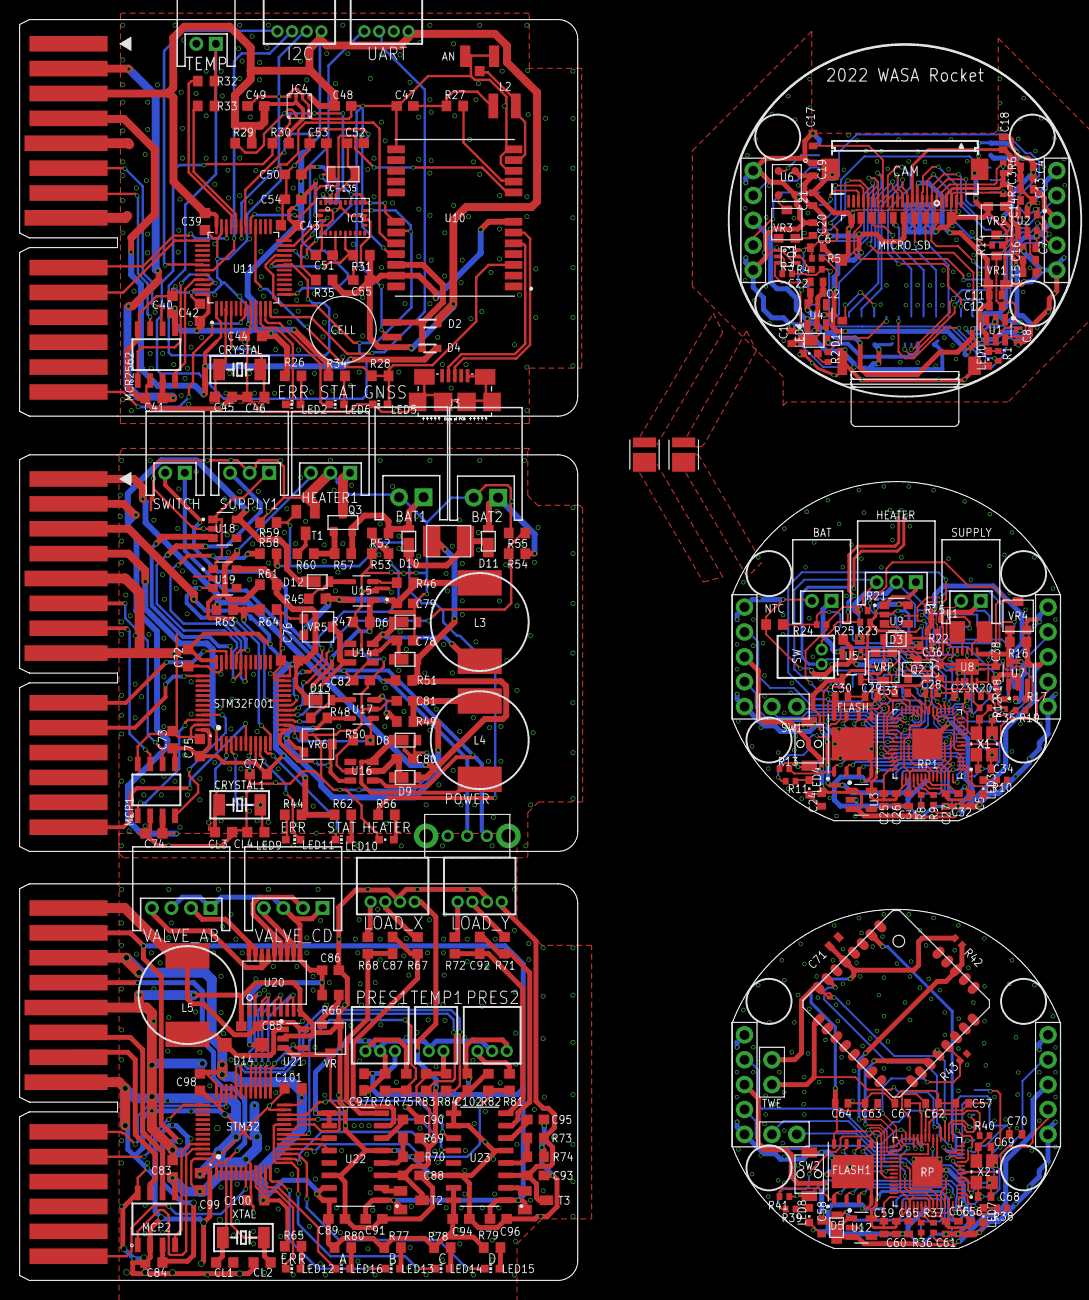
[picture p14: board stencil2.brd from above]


Board: 2 copper layers, 107.2 x 128.8 mm, 331 parts (10 on the bottom side), 303 nets.

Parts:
AB: S4B-PH-K-S
AN: U.FL-R-SMT; U.FL_SMT
BAT: S2B-PH-K-S
BAT1, BAT2: S2B-XH-A
BOTTOM, BOTTOM1: P5_2.54
C1, C4, C6, C7, C13, C18, C19, C24, C37, C58: 0.1µF; C0402
C2, C21, C25, C30, C36, C38, C59: 10µF; C0402
C3: 22µF; C0402
C5, C23, C27, C28, C29, C32, C33, C56, C57, C61, C62, C63, C70, C71: 0.1µ; C0402
C8, C14: 0.01µF; C0402
C9, C10: P5_2.54
C11, C20: 2.2µF; C0402
C12, C16: 100pF; C0402
C15: 1.0µF; C0402
C17: 15pF; C0402
C22: 1µF; C0402
C26, C31, C60, C65: 1µ; C0402
C34, C35: 10p; C0402
C39, C40, C41, C42, C43, C44, C72, C73, C74, C75, C76, C77, C83, C84, C98, C99, C100, C101: C0603K
C45, C46: 15pF; C0603K
C47: 47pF; C0603
C48, C49, C50, C51, C55: 0.1µ; C0603
C52, C53, C97, C102: C0603
C54, C82, C87, C89, C90, C92, C94, C95: 0.1µF; C0603
C64, C68, C69: 0.1μ; C0402
C66, C67: 1μ; C0402
C78, C79, C80, C81: 47µF; C0603
C85: 4.7µF; C0603
C86: 2.2µF; C0603
C88, C91, C93, C96: 10µF; C0603
CAM: OV2640_FPC_INV; FH12-24S-0.5SH
CD: S4B-PH-K-S
CELL: DCK-3R3E; DC,DCK
CL1, CL2, CL3, CL4: 15pF; C0603K
CRYSTAL, CRYSTAL1: 32.768kHz; FC-255
D1, D3, D5, D6, D7, D8, D9, D10, D11, D12, D13: CUHS20S30
D2, D4: RB521S-30TE61; SODFL1608X70N
D14: SOD123
ESP32: ESP32-S3-WROOM-1-N16R2; XCVR_ESP32-S3-WROOM-1-N16R2
FC-135: FC-135
FLASH, FLASH1: W25Q32JVZPIQ; SON127P600X500X80-9N
HEATER, HEATER1: S3B-PH-K-S
I2C: S4B-ZR
IC1, IC2: 4066D; SO14
IC3: BN055; LGA-28_3.80X5.20/0.5
IC4: BME280
J1, J2, J3, J4: MICRO_USB_B_HIROSE_ZX62-B-5PA(11)MODEL; GHI-CONNECTORS_10118192-0001LF(MICRO-USB-B-AMPHENOL-FCI)
L1: 4.7µH; L3225M
L2: 33Ω; SM-NE29
L3, L4: 22µH; NR10050
L5: 10µH; NR10050
LED0, LED1, LED3, LED4, LED7, LED8, LED10: CHIPLED_0603
LED2, LED5, LED6, LED9, LED11, LED12, LED13, LED14, LED15, LED16: CHIP-LED0603
LOAD_X: S4B-ZR
LOAD_Y: S4B-ZR
MCP1, MCP2, MCP2562: MCP2562-E/SN; SOIC127P600X175-8N
MICRO_SD: DM3AT-SF-PEJM5; HRS_DM3AT-SF-PEJM5
NTC: 10k; R0603
POWER: SK-12D01-VG4
PRES1, PRES2: S3B-ZR
PROG: THAF01-NC-R
Q1: HN1C01FU; SOT-363
Q2, Q3: IRLML6402; SOT-23
R1, R2, R12, R13, R14, R38, R39, R40, R41: 1k; R0402
R3, R4, R5, R6, R7, R18, R21, R24, R42, R43: 10k; R0402
R8, R9: 27.4; R0402
R10, R17, R23: 100; R0402
R11: 220; R0402
R15, R19, R20, R22: 100k; R0402
R16, R25, R45, R48: 0.033; R0603
R26, R28, R29, R30, R31, R34, R35: R0603
R27: 10; R0603
R32, R47, R50, R51, R57, R59, R61, R70, R74, R75, R81, R83: 10k; R0603
R33, R53, R55, R64, R84: 100k; R0603
R36, R37: 27Ω; R0402
R44, R58, R60, R62, R65, R77, R78, R79, R80: 1k; R0603
R46, R49, R67, R68, R71, R72: 100; R0603
R52, R54, R63, R66: 1M; R0603
R56: 470; R0603
R69, R73: 22k; R0603
R76, R82: 15k; R0603
RESET: THAF01-NC-R
RP, RP1: RP2040; QFN40P700X700X90-57N
S1: SSAJ120100
STM32, STM32F001: STM32F072-LQFP48; LQFP48
SUPPLY: S2B-PH-K-S
SUPPLY1: S3B-PH-K-S
SW: S2B-ZR
SW1, SW2: TVAF06-A020B-R
SWITCH: S2B-PH-K-S
T1: SOT23-EBC
T2, T3: SOT23-BEC
TEMP: S2B-PH-K-S
TEMP1: S2B-ZR
TOP, TOP1: P5_2.54
TWE: P2_2_2.54; P2_2.54
U1, U2: NJM11100; SOT95P240X110-6N
U3, U4, U12: NJM12888F; SOT95P240X110-5N
U5: MCP73831; SOT23-5L
U6: SPU0414HR5H-SB
U7, U15, U17: LT6106CS5#PBF; SOT95P280X100-5N_LT6106CS5#PBF
U8: TPS63000; 10-VFDFN
U9, U18, U19: TCK106AF,LF; IC_TCK106AF,LF
U10: NEO-M9N-00B; XCVR_NEO-M9N-00B
U11: STM32L433CCT6; QFP50P900X900X160-48N
U13: E220-900T22S
U14, U16: LT1616ES6TRMPBF; SOT-6_S
U20: TD62083AFNG; SSOP18-P-225-0.65
U21: LT1930; SOT95P240X110-5N
U22, U23: HX711; SOP127P600X180-16N
U$1, U$7, U$9: EDGE30
U$2, U$5: P2_2_2.54; P2_2.54
U$3, U$4: S1S0-3030XX9506
U$6: LITE
U$8: SMD1812P125TS; SMD1812P
UART: S4B-ZR
VR, VR1, VR2, VR3: 100k; PVZ3A
VR4, VR5, VR6: 22k; PVZ3A
VRP: 10k; PVZ3A
X1, X2: FA-238
XTAL: 32.768kHz; FC-255

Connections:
1.5V: C11.1, C12.1, CAM.10, U1.4, VR1.1
1PPS: LED5.A, R28.1, R28.2, U10.3, U11.28
1V1: C65.1, C66.1, C67.1, RP.23, RP.45, RP.50
1V2: C31.1, C32.1, C33.1, RP1.23, RP1.45, RP1.50
2.8V: C15.1, C16.1, C18.1, CAM.4, CAM.11, R6.1, R7.2, U2.4, VR2.1
3V3: C81.1, L4.2, R48.1, R49.2, U17.5, VR6.3
5V: C79.1, L3.2, R45.1, R46.2, U15.5, VR5.3
!SHDN!: C82.1, POWER.B, SWITCH.2, U14.4, U16.4
ADC0_IN: IC1.2, IC1.3, RP1.38
ADC1_IN: IC1.9, IC1.10, RP1.39
ADC2_IN: IC2.2, IC2.3, IC2.9, RP1.40
ADC_SEL1: IC1.6, IC1.13, IC2.13, RP1.16
ADC_SEL2: IC1.5, IC1.12, IC2.5, RP1.31
ADC_SEL3: IC2.6, RP1.29
ANT: AN.SIG, L2.2, U10.11
A_OUT: AB.2, U20.P17, U20.P18
BAT1: BAT1.1, D10.A, Q3.P2, R52.2, R57.2
BAT1_V: R52.1, R53.2, STM32F001.18
BAT2: BAT2.1, D11.A, R54.2
BAT2_V: R54.1, R55.2, STM32F001.17
BAT_V: IC1.4, R19.1, R20.2
BNO_!RESET!: IC3.11, R31.1, U11.20
B_OUT: AB.4, U20.P15, U20.P16
CAM_POWER: ESP32.37, U1.1, U2.1
CAM_RESET: CAM.6, ESP32.6
CANH1: MCP2562.7, U$1.7
CANH2: MCP1.7, U$7.7
CANH3: MCP2.7, U$9.7
CANL1: MCP2562.6, U$1.6
CANL2: MCP1.6, U$7.6
CANL3: MCP2.6, U$9.6
CAN_RX: MCP2562.4, U11.45
CAN_RX1: MCP1.4, STM32F001.45
CAN_RX2: MCP2.4, STM32.45
CAN_TX: MCP2562.1, U11.46
CAN_TX1: MCP1.1, STM32F001.46
CAN_TX2: MCP2.1, STM32.46
CHARGE: RP1.18, U5.1
C_OUT: CD.2, U20.P13, U20.P14
D0: CAM.19, ESP32.32
D1: CAM.21, ESP32.34
D2: CAM.22, ESP32.35
D3: CAM.20, ESP32.33
D4: CAM.18, ESP32.31
D5: CAM.16, ESP32.16
D6: CAM.14, ESP32.26
D7: CAM.12, ESP32.24
D_OUT: CD.4, U20.P11, U20.P12
EN: C6.1, ESP32.3, Q1.6, R5.1, RESET.3, RESET.4
EN1: C37.1, S1.2, SW.2, U8.6, U8.7, U8.8
GND: C1.2, C2.2, C3.2, C4.2, C6.2, C7.2, C8.2, C9.1, C9.5, C10.1, C10.5, C11.2, C13.2, C14.2, C15.2, C17.2, C18.2, C19.2, C20.2, C21.2, C22.2, CAM.2, CAM.15, CAM.PAD1, CAM.PAD2, ESP32.1, ESP32.40, ESP32.41_1, ESP32.41_2, ESP32.41_3, ESP32.41_4, ESP32.41_5, ESP32.41_6, ESP32.41_7, ESP32.41_8, ESP32.41_9, J1.CGND1, J1.CGND2, J1.CGND3, J1.CGND4, J1.CGND5, J1.CGND6, J1.GND, LED0.C, LED1.C, MICRO_SD.6, MICRO_SD.P1, MICRO_SD.P2, MICRO_SD.P3, MICRO_SD.P4, MICRO_SD.SWB, Q1.1, Q1.4, R14.2, RESET.1, RESET.2, U1.2, U2.2, U4.2, U6.2, VR1.3, VR2.3
GND1: BAT.2, BOTTOM.1, BOTTOM.5, C5.2, C23.2, C24.2, C25.2, C26.2, C27.2, C28.2, C29.2, C30.2, C31.2, C32.2, C33.2, C34.2, C35.2, C36.2, C37.2, C38.2, FLASH.4, FLASH.9, IC1.7, IC2.7, J2.CGND1, J2.CGND2, J2.CGND3, J2.CGND4, J2.CGND5, J2.CGND6, J2.GND, LED3.C, LED4.C, NTC.1, R18.1, R20.1, R22.1, R25.1, RP1.19, RP1.57, SUPPLY.2, SW1.P$1, TOP.1, TOP.5, U3.2, U5.2, U7.2, U8.3, U8.9, U8.P$1, U8.P$2, U8.P$3, U8.P$4, U8.P$5, U9.2, VR4.3, VRP.1, X1.2, X1.4
GND2: AN.GND1, AN.GND2, C39.2, C40.2, C41.2, C42.2, C43.2, C44.2, C45.1, C46.1, C47.2, C48.2, C49.2, C50.2, C51.2, C52.1, C53.1, C54.2, C55.2, CELL.-, I2C.2, IC3.2, IC3.5, IC3.6, IC3.17, IC3.18, IC3.25, IC4.1, IC4.5, IC4.7, J3.CGND1, J3.CGND2, J3.CGND3, J3.CGND4, J3.CGND5, J3.CGND6, J3.GND, LED5.C, MCP2562.2, MCP2562.8, TEMP.2, U10.10, U10.12, U10.13, U10.24, U11.8, U11.23, U11.35, U11.47, U$1.5, U$1.8, UART.2
GND3: BOTTOM1.1, BOTTOM1.5, C56.2, C57.2, C58.2, C59.2, C60.2, C61.2, C62.2, C63.2, C64.2, C65.2, C66.2, C67.2, C68.2, C69.2, C70.2, C71.2, FLASH1.4, FLASH1.9, J4.CGND1, J4.CGND2, J4.CGND3, J4.CGND4, J4.CGND5, J4.CGND6, J4.GND, LED7.C, LED8.C, R43.1, RP.19, RP.57, SW2.P$1, TOP1.1, TOP1.5, U12.2, U13.P1, U13.P2, U13.P3, U13.P4, U13.P11, U13.P13, U13.P19, U13.P20, U13.P22, U$6.20, U$6.28, X2.2, X2.4
GND4: BAT1.2, BAT2.2, C72.2, C73.2, C74.2, C75.2, C76.2, C77.2, C78.2, C79.2, C80.2, C81.2, C82.2, CL3.1, CL4.1, D6.A, D8.A, HEATER1.2, LED10.C, MCP1.2, MCP1.8, R47.1, R50.1, R53.1, R55.1, R59.1, R64.1, STM32F001.8, STM32F001.23, STM32F001.35, STM32F001.47, SUPPLY1.2, T1.E, U14.2, U15.2, U16.2, U17.2, U18.2, U19.2, U$7.5, U$7.8, VR5.1, VR6.1
GND5: C83.2, C84.2, C85.2, C86.2, C88.2, C89.2, C90.2, C91.2, C93.2, C94.2, C95.2, C96.2, C97.2, C98.2, C99.2, C100.2, C101.2, C102.2, CL1.1, CL2.1, LOAD_X.2, LOAD_Y.2, MCP2.2, MCP2.8, PRES1.2, PRES2.2, R70.1, R74.1, R76.1, R82.1, STM32.8, STM32.23, STM32.35, STM32.47, TEMP1.2, U20.P9, U21.2, U22.5, U22.9, U22.10, U22.14, U23.5, U23.9, U23.10, U23.14, U$9.5, U$9.8, VR.1
GPS_!RESET!: U10.8, U11.29
GPS_RTX: U10.20, U11.31
GPS_TRX: U10.21, U11.30
HEATER: RP1.17, U9.3
HEATER1: R58.1, STM32F001.30
HEATER+: HEATER1.1, Q3.P3
HEATER_I: HEATER.2, IC1.11, R25.2
HEATER_OUT: HEATER.1, U9.1
HSYNC: CAM.9, ESP32.8
I2C1_SCL: I2C.4, U11.42
I2C1_SDA: I2C.3, U11.43
I2C2_SCL: IC3.19, IC4.4, R30.1, U10.19, U11.21
I2C2_SDA: IC3.20, IC4.3, R29.1, U10.18, U11.22
I2C_SCL: CAM.5, ESP32.4, R6.2
I2C_SDA: CAM.3, ESP32.5, R7.1
IO0: C22.1, ESP32.27, Q1.3
LED0: ESP32.21, R1.2
LED1: ESP32.22, R2.2
LED2: R10.2, RP1.2
LED3: R11.2, RP1.37
LED4: R38.2, RP.2
LED5: R39.2, RP.37
LORA_AUX: RP.14, U13.P9
LORA_M0: RP.9, U13.P5
LORA_M1: RP.11, U13.P6
LORA_RTX: RP.16, U13.P8
LORA_TRX: RP.15, U13.P7
MIC: ESP32.39, U6.4
unnamed: C8.1, U1.3
unnamed: C12.2, U1.5, VR1.2
unnamed: C14.1, U2.3
unnamed: C16.2, U2.5, VR2.2
unnamed: PROG.3, PROG.4, R3.1, R4.1
unnamed: LED3.A, R10.1
unnamed: LED0.A, R1.1
unnamed: LED1.A, R2.1
unnamed: Q1.2, R3.2
unnamed: CAM.8, R14.1
unnamed: Q1.5, R4.2
unnamed: LED4.A, R11.1
unnamed: U6.3, VR3.2
unnamed: C20.1, VR3.3
unnamed: C35.1, R12.1, X1.1
unnamed: U5.5, VRP.2
unnamed: R17.1, U7.3
unnamed: L1.1, U8.4
unnamed: L1.2, U8.2
unnamed: R23.2, S1.C, SW.1
unnamed: U11.7, U$1.15
unnamed: R27.2, U10.9
unnamed: C47.1, L2.1, R27.1
unnamed: CELL.+, D2.1, D4.1, U10.22
unnamed: C51.1, IC3.9
unnamed: C53.2, FC-135.P$2, IC3.27
unnamed: C52.2, FC-135.P$1, IC3.26
unnamed: LED6.C, U11.11
unnamed: LED6.A, R34.2
unnamed: IC3.4, R35.1
unnamed: LED2.C, U11.10
unnamed: D5.A, J4.VBUS
unnamed: LED7.A, R38.1
unnamed: LED8.A, R39.1
unnamed: C69.1, R40.1, X2.1
unnamed: CL4.2, CRYSTAL1.1, STM32F001.4
unnamed: R46.1, U15.3
unnamed: R49.1, U17.3
unnamed: POWER.C, R51.1, SWITCH.1
unnamed: SUPPLY1.1, U18.1, U19.1
unnamed: LED10.A, R56.2
unnamed: Q3.P1, R57.1, R60.1
unnamed: R56.1, R58.2, R59.2, T1.B
unnamed: R60.2, T1.C
unnamed: LED11.C, STM32F001.11
unnamed: LED11.A, R62.2
unnamed: LED12.C, STM32.10
unnamed: LED12.A, R65.2
unnamed: D14.A, L5.2, U21.1
unnamed: R66.1, VR.3
unnamed: C87.2, R67.1, U22.7
unnamed: C87.1, R68.1, U22.8
unnamed: T2.B, U22.2
unnamed: C90.1, U22.6
unnamed: R69.1, R70.2, U22.4
unnamed: C92.2, R71.1, U23.7
unnamed: C92.1, R72.1, U23.8
unnamed: T3.B, U23.2
unnamed: C95.1, U23.6
unnamed: R73.1, R74.2, U23.4
unnamed: PRES1.3, R75.2
unnamed: LED13.C, STM32.12
unnamed: LED13.A, R77.2
unnamed: LED14.C, STM32.20
unnamed: LED14.A, R78.2
unnamed: C46.2, CRYSTAL.1, U11.4
unnamed: C45.2, CRYSTAL.2, U11.3
unnamed: CL3.2, CRYSTAL1.2, STM32F001.3
unnamed: LED9.C, STM32F001.10
unnamed: LED2.A, R26.2
unnamed: LED15.C, STM32.14
unnamed: LED9.A, R44.2
unnamed: LED15.A, R79.2
unnamed: CL2.2, STM32.4, XTAL.1
unnamed: CL1.2, STM32.3, XTAL.2
unnamed: LED16.C, STM32.11
unnamed: LED16.A, R80.2
unnamed: PRES2.3, R81.2
NRST: STM32.7, U$9.15
NRST1: STM32F001.7, U$7.15
OB_TEMP: IC2.8, NTC.2, R24.1
PCLK: C17.1, CAM.17, ESP32.15
POWER_FB: STM32.19, U21.3, VR.2
POWER_ON: STM32.25, U21.4
PRESSURE_1: R75.1, R76.2, STM32.18
PRESSURE_2: R81.1, R82.2, STM32.15
QSPI_SCLK: FLASH.6, RP1.52
QSPI_SCLK1: FLASH1.6, RP.52
QSPI_SD0: FLASH.5, RP1.53
QSPI_SD1: FLASH.2, RP1.55
QSPI_SD2: FLASH.3, RP1.54
QSPI_SD3: FLASH.7, RP1.51
QSPI_SD4: FLASH1.5, RP.53
QSPI_SD5: FLASH1.2, RP.55
QSPI_SD6: FLASH1.3, RP.54
QSPI_SD7: FLASH1.7, RP.51
QSPI_SS: FLASH.1, R13.2, RP1.56
QSPI_SS1: FLASH1.1, R41.2, RP.56
RX0: C9.4, ESP32.36
RX1: C10.4, ESP32.10
RX2: RP1.28, TOP.4
RX3: BOTTOM.4, RP1.7
RX4: RP.28, TOP1.4
RX5: BOTTOM1.4, RP.7
SD: ESP32.23, MICRO_SD.SWA
SDIO_D1: ESP32.12, MICRO_SD.8
SDIO_D2: ESP32.11, MICRO_SD.1
SPI0_CS: ESP32.17, MICRO_SD.2
SPI0_MISO: ESP32.20, MICRO_SD.7
SPI0_MOSI: ESP32.18, MICRO_SD.3
SPI0_SCK: ESP32.19, MICRO_SD.5
SUPPLY_3V3: STM32F001.32, U19.3
SUPPLY_5V: STM32F001.33, U18.3
SUPPLY_CON: STM32F001.31, SUPPLY1.3
SUPPLY_V: IC1.1, R15.1, R22.2
SW: R13.1, RP1.35, SW1.P$2
SW1: R41.1, RP.35, SW2.P$2
SWCLK: RP1.24, U$2.P$1
SWCLK1: U11.37, U$1.11
SWCLK2: RP.24, U$5.P$1
SWCLK3: STM32F001.37, U$7.11
SWCLK4: STM32.37, U$9.11
SWD: RP1.25, U$2.P$2
SWD1: RP.25, U$5.P$2
SWDIO1: U11.34, U$1.10
SWDIO2: STM32F001.34, U$7.10
SWDIO3: STM32.34, U$9.10
TEMP: HEATER.3, IC2.4, R21.1
TEMP1: R32.1, R33.1, TEMP.1, U11.19
TEMP2: HEATER1.3, R61.1, STM32F001.12
TEMP3: R83.1, R84.1, STM32.13, TEMP1.1
TEMP_HIGH: R32.2, U11.33
TEMP_HIGH1: R83.2, STM32.32
TEMP_LOW: R33.2, U11.32
TEMP_LOW1: R84.2, STM32.31
TWE_BPS: RP.31, U$6.19
TWE_PGM: RP.12, U$6.2
TWE_RESET: R43.2, RP.30, U$6.21
TWE_RTS: RP.13, U$6.7
TWE_RTX: RP.17, TWE.P$2, U$6.8
TWE_SLEEP: R42.1, RP.29, U$6.27
TWE_TRX: RP.18, TWE.P$1, U$6.9
TX0: C9.2, ESP32.38
TX1: C10.2, ESP32.9
TX2: RP1.27, TOP.2
TX3: BOTTOM.2, RP1.6
TX4: RP.27, TOP1.2
TX5: BOTTOM1.2, RP.6
UART_RTX: U11.13, UART.4
UART_TRX: U11.12, UART.3
USB_D+: J3.D+, U10.6
USB_D-: J3.D-, U10.5
USB_DM: ESP32.13, J1.D-
USB_DM1: J2.D-, R8.2
USB_DM2: J4.D-, R36.2
USB_DM_1: R8.1, RP1.46
USB_DM_2: R36.1, RP.46
USB_DP: ESP32.14, J1.D+
USB_DP1: J2.D+, R9.2
USB_DP2: J4.D+, R37.2
USB_DP_1: R9.1, RP1.47
USB_DP_2: R37.1, RP.47
USB_VCC: D1.A, J1.VBUS
V+: C1.1, C7.1, C9.3, C10.3, C13.1, D1.C, U1.6, U2.6, U4.1, U4.3
V+1: BOTTOM.3, C24.1, R16.2, TOP.3, U3.1, U3.3, U7.4
V+2: BOTTOM1.3, C58.1, D5.C, TOP1.3, U12.1, U12.3
V+3: STM32.1, U$9.4
V+_I: IC1.8, R18.2, U7.1
V+_V: IC2.1, U8.10, VR4.2
VALVE_A: STM32.29, U20.P1, U20.P2
VALVE_B: STM32.28, U20.P3, U20.P4
VALVE_C: STM32.27, U20.P5, U20.P6
VALVE_D: STM32.26, U20.P7, U20.P8
VBAT: BAT.1, Q2.P3, R19.2, U5.3
VBAT1: D4.2, U11.1, U$1.4
VBAT2: STM32F001.1, U$7.4
VBAT_: C36.1, D3.C, Q2.P2, R23.1, U8.5, U9.5
VCC: C41.1, MCP2562.3, U$1.2
VCC1: C74.1, D12.C, MCP1.3, U18.5, U$7.2
VCC2: C84.1, C91.1, C96.1, C97.1, C102.1, MCP2.3, PRES1.1, PRES2.1, T2.E, T3.E, U22.1, U23.1, U$9.2
VCC': D12.A, R45.2, U15.4
VCC_I: R47.2, STM32F001.16, U15.1
VCC_IN: C78.1, D7.C, U14.5
VCC_SW: D6.C, L3.1, U14.6
VCC_V: STM32F001.15, U14.3, VR5.2
VDD: C2.1, C3.1, C4.1, C19.1, C21.1, ESP32.2, MICRO_SD.4, PROG.1, PROG.2, R5.2, U4.5, U6.1
VDD1: C5.1, C23.1, C25.1, C26.1, C27.1, C28.1, C29.1, C30.1, FLASH.8, IC1.14, IC2.14, R21.2, R24.2, RP1.1, RP1.10, RP1.22, RP1.26, RP1.33, RP1.42, RP1.43, RP1.44, RP1.48, RP1.49, U3.5
VDD2: C39.1, C40.1, C42.1, C43.1, C44.1, C48.1, C49.1, C50.1, C54.1, C55.1, D2.2, I2C.1, IC3.3, IC3.28, IC4.2, IC4.6, IC4.8, MCP2562.5, R26.1, R29.2, R30.2, R31.2, R34.1, R35.2, U10.7, U10.23, U11.9, U11.24, U11.36, U11.48, U$1.3, UART.1
VDD3: C56.1, C57.1, C59.1, C60.1, C61.1, C62.1, C63.1, C64.1, C70.1, C71.1, FLASH1.8, R42.2, RP.1, RP.10, RP.22, RP.26, RP.33, RP.42, RP.43, RP.44, RP.48, RP.49, U12.5, U13.P10, U$6.5
VDD4: C72.1, C73.1, C75.1, C76.1, C77.1, D13.C, MCP1.5, R44.1, R61.2, R62.1, STM32F001.9, STM32F001.24, STM32F001.36, STM32F001.48, U19.5, U$7.3
VDD5: C83.1, C89.1, C94.1, C98.1, C99.1, C100.1, C101.1, MCP2.5, R65.1, R77.1, R78.1, R79.1, R80.1, STM32.9, STM32.24, STM32.36, STM32.48, U22.15, U22.16, U23.15, U23.16, U$9.3
VDD': D13.A, R48.2, U17.4
VDD_I: R50.2, STM32F001.14, U17.1
VDD_IN: C80.1, D9.C, U16.5
VDD_SW: D8.C, L4.1, U16.6
VDD_V: STM32F001.13, U16.3, VR6.2
VOUT: C38.1, R16.1, R17.2, U7.5, U8.1, VR4.1
VPP: D3.A, J2.VBUS, Q2.P1, R15.2, SUPPLY.1, U5.4
VPP2: D7.A, D9.A, R51.2, R63.2, U$7.1, U$8.2
VPP3: C85.1, L5.1, U21.5, U$9.1
VPP_IN: D10.C, D11.C, U$8.1
VPP_V: R63.1, R64.2, STM32F001.19
VSYNC: CAM.7, ESP32.7
V_VALVE: AB.1, AB.3, C86.1, CD.1, CD.3, D14.C, R66.2, U20.P10
XCLK: CAM.13, ESP32.25
XIN1: C34.1, RP1.20, X1.3
XIN2: C68.1, RP.20, X2.3
XOUT1: R12.2, RP1.21
XOUT2: R40.2, RP.21
X_DATA: STM32.16, U22.12
X_SCK: STM32.17, U22.11
X_SIG+: LOAD_X.4, R68.2
X_SIG-: LOAD_X.3, R67.2
X_VDD: C88.1, LOAD_X.1, R69.2, T2.C, U22.3
Y_DATA: STM32.21, U23.12
Y_SCK: STM32.22, U23.11
Y_SIG+: LOAD_Y.4, R72.2
Y_SIG-: LOAD_Y.3, R71.2
Y_VDD: C93.1, LOAD_Y.1, R73.2, T3.C, U23.3

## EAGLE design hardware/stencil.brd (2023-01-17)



Board: 2 copper layers, 111.6 x 73.5 mm, 271 parts (8 on the bottom side), 247 nets.

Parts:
BAT, BAT2: MS414GE-FL26E; BAT_MS414GE-FL26E
BAT1: S2B-PH-K-S
BOTTOM, BOTTOM1, BOTTOM2, BOTTOM3, BOTTOM4: P5_2.54
C1, C18, C23, C24, C25, C26, C30, C35, C36, C41, C57, C72, C86, C87, C90: 0.1µF; C0402
C2, C19, C38, C42, C58, C63, C73, C84, C91: 10µF; C0402
C3, C4, C43, C48, C59, C64, C74, C79, C92, C97: 1µ; C0402
C5, C6: 1μ; C0402
C7, C8, C9, C10, C11, C15, C16, C17, C39, C40, C44, C45, C46, C53, C54, C55, C56, C60, C61, C62, C65, C66, C70, C71, C75, C76, C77, C88, C89, C93, C94, C95, C102, C103, C104, C107: 0.1µ; C0402
C12, C13, C14: 0.1μ; C0402
C20, C21: P5_2.54
C22: 22µF; C0402
C27, C31: 0.01µF; C0402
C28, C37: 2.2µF; C0402
C29, C33: 100pF; C0402
C32: 1.0µF; C0402
C34: 15pF; C0402
C47, C49, C50, C51, C52, C78, C80, C81, C82, C83, C85, C96, C98, C99, C100, C101, C108, C109: C0402
C67, C68: 10p; C0402
C69: 153CLV-0605
C105: 6.8n; C0402
C106: 0.12u; C0402
CAM: OV2640_FPC_INV; FH12-24S-0.5SH
D1, D2, D3, D4, D5, D6, D7, D8, D9: CUHS20S30
ESP32: ESP32-S3-WROOM-1-N16R2; XCVR_ESP32-S3-WROOM-1-N16R2
FC-135: FC-135
FLASH, FLASH1, FLASH2, FLASH3, FLASH4: W25Q32JVZPIQ; SON127P600X500X80-9N
FLASH_LOG: W25Q32JVZPIQ; SON127P600X500X80-9N
GNSS: GYSFDMAXB
HEATER: S3B-PH-K-S
I2C: B4B-PH-K-S
IC1: BN055; LGA-28_3.80X5.20/0.5
IC2: BME280
J1, J2, J3, J4, J5, J6: MICRO_USB_B_HIROSE_ZX62-B-5PA(11)MODEL; GHI-CONNECTORS_10118192-0001LF(MICRO-USB-B-AMPHENOL-FCI)
LED0, LED1, LED2, LED3, LED4, LED5, LED6, LED7, LED8, LED9, LED10, LED11, LED12: CHIPLED_0603
MICRO_SD, MICRO_SD1: DM3AT-SF-PEJM5; HRS_DM3AT-SF-PEJM5
Q1: HN1C01FU; SOT-363
Q2: IRLML6402; SOT-23
Q3: IRLML6344; SOT-23
R1, R2: 27Ω; R0402
R3, R4, R5, R6, R18, R25, R26, R32, R33, R45, R46, R51, R52: 1k; R0402
R7, R8, R9, R10, R11, R14, R15, R16, R17, R19, R20, R37: 10k; R0402
R12, R13, R21, R22, R23, R24, R41, R42, R43, R44, R47, R48, R49, R50, R55, R56, R57, R58, R59: R0402
R27, R30, R36: 100; R0402
R28, R29: 27.4; R0402
R31: 220; R0402
R34, R38, R39: 100k; R0402
R35: 0.033; R0603
R40, R53, R54: 22k; R0402
RP, RP1, RP2, RP3, RP4: RP2040; QFN40P700X700X90-57N
RPROG: 10k; PVZ3A
SUPPLY: S2B-PH-K-S
SW, SW1, SW2, SW3, SW4: TVAF06-A020B-R
TMP0, TMP1: S2B-PH-K-S
TOP, TOP1, TOP2, TOP3, TOP4: P5_2.54
TWE: P2_2_2.54; P2_2.54
U1: ES920LR3
U2, U4, U8, U9, U12, U14: NJM12888F; SOT95P240X110-5N
U3, U5: NJM11100; SOT95P240X110-6N
U6: SPU0414HR5H-SB
U7: FT234XD-R; SON45P300X300X80-13N
U10: MCP73831; SOT23-5L
U11: LT6106CS5#PBF; SOT95P280X100-5N_LT6106CS5#PBF
U13: RX-8035LC; VSOJ12
U$1: LITE
U$2, U$3, U$4, U$5, U$6: P2_2_2.54; P2_2.54
VR1, VR2: PVZ3A
VR3: 100k; PVZ3A
X1, X2, X3, X4, X5: FA-238

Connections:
1.3V: C28.1, C29.1, CAM.10, U3.4, VR1.1
1V1: C48.1, C49.1, C50.1, RP1.23, RP1.45, RP1.50
1V2: C4.1, C5.1, C6.1, RP.23, RP.45, RP.50
1V3: C64.1, C65.1, C66.1, RP2.23, RP2.45, RP2.50
1V4: C79.1, C80.1, C81.1, RP3.23, RP3.45, RP3.50
1V5: C97.1, C98.1, C99.1, RP4.23, RP4.45, RP4.50
2.8V: C32.1, C33.1, C35.1, CAM.4, CAM.11, R19.1, R20.2, U5.4, VR2.1
BOOT_LOAD: IC1.4, R58.1
CAM_RESET: CAM.6, ESP32.6
D0: CAM.19, ESP32.32
D1: CAM.21, ESP32.34
D2: CAM.22, ESP32.35
D3: CAM.20, ESP32.33
D4: CAM.18, ESP32.31
D5: CAM.16, ESP32.28
D6: CAM.14, ESP32.26
D7: CAM.12, ESP32.24
DTR: Q1.4, R15.1
EN: C25.1, ESP32.3, Q1.6, R17.1
GND: BOTTOM.1, BOTTOM.5, C1.2, C2.2, C3.2, C4.2, C5.2, C6.2, C7.2, C8.2, C9.2, C10.2, C11.2, C12.2, C13.2, C14.2, C15.2, C16.1, C17.2, FLASH.4, FLASH.9, J1.CGND1, J1.CGND2, J1.CGND3, J1.CGND4, J1.CGND5, J1.CGND6, J1.GND, LED1.C, LED2.C, R11.1, RP.19, RP.57, SW.P$1, TOP.1, TOP.5, U1.P1, U1.P15, U1.P31, U1.P32, U1.P33, U1.P34, U1.P35, U1.P36, U1.P37, U1.P38, U1.P39, U2.2, U$1.20, U$1.28, X1.2, X1.4
GND1: C18.2, C19.2, C20.1, C20.5, C21.1, C21.5, C22.2, C23.2, C24.2, C25.2, C26.2, C27.2, C28.2, C30.2, C31.2, C32.2, C34.2, C35.2, C36.2, C37.2, C38.2, CAM.2, CAM.15, CAM.PAD1, CAM.PAD2, ESP32.1, ESP32.40, ESP32.41_1, ESP32.41_2, ESP32.41_3, ESP32.41_4, ESP32.41_5, ESP32.41_6, ESP32.41_7, ESP32.41_8, ESP32.41_9, J2.CGND1, J2.CGND2, J2.CGND3, J2.CGND4, J2.CGND5, J2.CGND6, J2.GND, LED0.C, LED3.C, MICRO_SD.6, MICRO_SD.P1, MICRO_SD.P2, MICRO_SD.P3, MICRO_SD.P4, MICRO_SD.SWB, R18.2, U3.2, U4.2, U5.2, U6.2, U7.5, U7.13, VR1.3, VR2.3
GND2: BAT.-, BOTTOM1.1, BOTTOM1.5, C39.2, C40.2, C41.2, C42.2, C43.2, C44.2, C45.2, C46.2, C47.2, C48.2, C49.2, C50.2, C51.2, C52.2, C53.2, C54.2, FLASH1.4, FLASH1.9, GNSS.1, GNSS.2, GNSS.7, GNSS.10, GNSS.12, GNSS.19, GNSS.20, J3.CGND1, J3.CGND2, J3.CGND3, J3.CGND4, J3.CGND5, J3.CGND6, J3.GND, LED4.C, LED5.C, LED6.C, RP1.19, RP1.57, SW1.P$1, TOP1.1, TOP1.5, U8.2, X2.2, X2.4
GND3: BAT1.2, BOTTOM2.1, BOTTOM2.5, C55.2, C56.2, C57.2, C58.2, C59.2, C60.2, C61.2, C62.2, C63.2, C64.2, C65.2, C66.2, C67.2, C68.2, C69.-, FLASH2.4, FLASH2.9, J4.CGND1, J4.CGND2, J4.CGND3, J4.CGND4, J4.CGND5, J4.CGND6, J4.GND, LED7.C, LED8.C, Q3.P2, R34.1, R37.1, R39.1, R40.1, RP2.19, RP2.57, RPROG.1, SUPPLY.2, SW2.P$1, TOP2.1, TOP2.5, U9.2, U10.2, U11.2, X3.2, X3.4
GND4: BAT2.-, BOTTOM3.1, BOTTOM3.5, C70.2, C71.2, C72.2, C73.2, C74.2, C75.2, C76.2, C77.2, C78.2, C79.2, C80.2, C81.2, C82.2, C83.2, C84.2, C85.2, C86.2, C87.2, FLASH3.4, FLASH3.9, FLASH_LOG.4, FLASH_LOG.9, J5.CGND1, J5.CGND2, J5.CGND3, J5.CGND4, J5.CGND5, J5.CGND6, J5.GND, LED9.C, LED10.C, MICRO_SD1.6, MICRO_SD1.P1, MICRO_SD1.P2, MICRO_SD1.P3, MICRO_SD1.P4, MICRO_SD1.SWA, RP3.19, RP3.57, SW3.P$1, TOP3.1, TOP3.5, U12.2, U13.9, X4.2, X4.4
GND5: BOTTOM4.1, BOTTOM4.5, C88.2, C89.2, C90.2, C91.2, C92.2, C93.2, C94.2, C95.2, C96.2, C97.2, C98.2, C99.2, C100.2, C101.2, C102.2, C103.2, C104.2, C105.2, C106.2, C107.2, C108.1, C109.1, FLASH4.4, FLASH4.9, I2C.2, IC1.2, IC1.5, IC1.6, IC1.15, IC1.16, IC1.18, IC1.25, IC2.1, IC2.5, IC2.7, J6.CGND1, J6.CGND2, J6.CGND3, J6.CGND4, J6.CGND5, J6.CGND6, J6.GND, LED11.C, LED12.C, R53.1, R54.1, R59.1, RP4.19, RP4.57, SW4.P$1, TOP4.1, TOP4.5, U14.2, X5.2, X5.4
GPS_RESET: GNSS.4, RP1.14
GPS_RTX: GNSS.5, RP1.16
GPS_TRX: GNSS.3, RP1.15
HSYNC: CAM.9, ESP32.8
I2C0_SCL: RP3.12, U13.6
I2C0_SCL1: I2C.4, IC1.19, IC2.4, R56.1, RP4.18
I2C0_SDA2: RP3.11, U13.8
I2C0_SDA3: I2C.3, IC1.20, IC2.3, R55.1, RP4.17
I2C_SCL: CAM.5, ESP32.4, R19.2
I2C_SDA: CAM.3, ESP32.5, R20.1
INT: IC1.14, RP4.15
IO0: ESP32.27, Q1.3
ISENSE: R37.2, RP2.38, U11.1
LED0: R3.2, RP.2
LED1: R4.2, RP.37
LED2: ESP32.21, R12.2
LED3: ESP32.22, R13.2
LED4: R23.2, RP1.2
LED5: R24.2, RP1.37
LED6: R30.2, RP2.2
LED7: R31.2, RP2.37
LED8: R43.2, RP3.2
LED9: R44.2, RP3.37
LED10: R49.2, RP4.2
LED11: R50.2, RP4.37
MIC: ESP32.39, U6.4
unnamed: LED3.A, R13.1
unnamed: Q1.2, R15.2
unnamed: Q1.5, R16.2
unnamed: C27.1, U3.3
unnamed: D1.A, J1.VBUS
unnamed: LED0.A, R12.1
unnamed: LED1.A, R3.1
unnamed: LED2.A, R4.1
unnamed: C29.2, U3.5, VR1.2
unnamed: C13.1, R5.1, X1.1
unnamed: C31.1, U5.3
unnamed: C33.2, U5.5, VR2.2
unnamed: CAM.8, R18.1
unnamed: U6.3, VR3.2
unnamed: C37.1, VR3.3
unnamed: C24.1, U7.2, U7.3, U7.9
unnamed: D3.A, J3.VBUS
unnamed: LED4.A, R23.1
unnamed: LED5.A, R24.1
unnamed: C52.1, R25.1, X2.1
unnamed: BAT.+, C54.1, D4.C, GNSS.14
unnamed: LED6.A, R27.1
unnamed: GNSS.6, R27.2
unnamed: D5.A, J4.VBUS
unnamed: LED7.A, R30.1
unnamed: LED8.A, R31.1
unnamed: C68.1, R32.1, X3.1
unnamed: RPROG.2, U10.5
unnamed: R36.1, U11.3
unnamed: HEATER.3, Q3.P3
unnamed: D8.A, J5.VBUS
unnamed: LED9.A, R43.1
unnamed: LED10.A, R44.1
unnamed: C83.1, R45.1, X4.1
unnamed: BAT2.+, C86.1, U13.1, U13.4
unnamed: D9.A, J6.VBUS
unnamed: LED11.A, R49.1
unnamed: LED12.A, R50.1
unnamed: C101.1, R51.1, X5.1
unnamed: C107.1, IC1.9
unnamed: IC1.17, R59.2
unnamed: C109.2, FC-135.P$2, IC1.27
unnamed: C108.2, FC-135.P$1, IC1.26
PCLK: C34.1, CAM.17, ESP32.30
QSPI_SCLK: FLASH.6, RP.52
QSPI_SCLK1: FLASH1.6, RP1.52
QSPI_SCLK2: FLASH2.6, RP2.52
QSPI_SCLK3: FLASH3.6, RP3.52
QSPI_SCLK4: FLASH4.6, RP4.52
QSPI_SD0: FLASH.5, RP.53
QSPI_SD1: FLASH.2, RP.55
QSPI_SD2: FLASH.3, RP.54
QSPI_SD3: FLASH.7, RP.51
QSPI_SD4: FLASH1.5, RP1.53
QSPI_SD5: FLASH1.2, RP1.55
QSPI_SD6: FLASH1.3, RP1.54
QSPI_SD7: FLASH1.7, RP1.51
QSPI_SD8: FLASH2.5, RP2.53
QSPI_SD9: FLASH2.2, RP2.55
QSPI_SD10: FLASH2.3, RP2.54
QSPI_SD11: FLASH2.7, RP2.51
QSPI_SD12: FLASH3.5, RP3.53
QSPI_SD13: FLASH3.2, RP3.55
QSPI_SD14: FLASH3.3, RP3.54
QSPI_SD15: FLASH3.7, RP3.51
QSPI_SD16: FLASH4.5, RP4.53
QSPI_SD17: FLASH4.2, RP4.55
QSPI_SD18: FLASH4.3, RP4.54
QSPI_SD19: FLASH4.7, RP4.51
QSPI_SS: FLASH.1, R6.2, RP.56
QSPI_SS1: FLASH1.1, R26.2, RP1.56
QSPI_SS2: FLASH2.1, R33.2, RP2.56
QSPI_SS3: FLASH3.1, R46.2, RP3.56
QSPI_SS4: FLASH4.1, R52.2, RP4.56
RESET: IC1.11, R57.1, RP4.16
ROLA_!RESET!: R14.1, RP.11, U1.P30
ROLA_RTX: R8.1, RP.16, U1.P25
ROLA_TRX: R7.1, RP.15, U1.P26
RTS: Q1.1, R16.1, U7.8
RTX: ESP32.36, U7.7
RX0: RP.28, TOP.4
RX1: BOTTOM.4, RP.7
RX2: C20.4, ESP32.29
RX3: C21.4, ESP32.10
RX4: RP1.28, TOP1.4
RX5: BOTTOM1.4, RP1.7
RX6: RP2.28, TOP2.4
RX7: BOTTOM2.4, RP2.7
RX8: RP3.28, TOP3.4
RX9: BOTTOM3.4, RP3.7
RX10: RP4.28, TOP4.4
RX11: BOTTOM4.4, RP4.7
SD: ESP32.23, MICRO_SD.SWA
SD1: MICRO_SD1.SWB, RP3.14
SPI0_CS: ESP32.17, MICRO_SD.2
SPI0_CS3: MICRO_SD1.2, RP3.32
SPI0_MISO: ESP32.20, MICRO_SD.7
SPI0_MISO3: MICRO_SD1.7, RP3.31
SPI0_MOSI: ESP32.18, MICRO_SD.3
SPI0_MOSI3: MICRO_SD1.3, RP3.30
SPI0_SCK: ESP32.19, MICRO_SD.5
SPI0_SCK3: MICRO_SD1.5, RP3.29
SPI1_CS1: FLASH_LOG.1, RP3.16
SPI1_MISO1: FLASH_LOG.2, RP3.15
SPI1_MOSI2: FLASH_LOG.5, RP3.18
SPI1_SCK2: FLASH_LOG.6, RP3.17
SW: R6.1, RP.35, SW.P$2
SW1: R26.1, RP1.35, SW1.P$2
SW2: R33.1, RP2.35, SW2.P$2
SW3: R46.1, RP3.35, SW3.P$2
SW4: R52.1, RP4.35, SW4.P$2
SWCLK: RP.24, U$2.P$1
SWCLK1: RP1.24, U$3.P$1
SWCLK2: RP2.24, U$4.P$1
SWCLK3: RP3.24, U$5.P$1
SWCLK4: RP4.24, U$6.P$1
SWD: RP.25, U$2.P$2
SWD1: RP1.25, U$3.P$2
SWD2: RP2.25, U$4.P$2
SWD3: RP3.25, U$5.P$2
SWD4: RP4.25, U$6.P$2
T0: R54.2, RP4.38, TMP1.2
T1: R53.2, RP4.39, TMP0.2
TEMP: HEATER.2, R40.2, RP2.40
TRX: ESP32.37, U7.10
TWE_BPS: RP.31, U$1.19
TWE_PGM: RP.12, U$1.2
TWE_RESET: R11.2, RP.30, U$1.21
TWE_RTS: RP.13, U$1.7
TWE_RTX: RP.17, TWE.P$2, U$1.8
TWE_SLEEP: R10.1, RP.29, U$1.27
TWE_TRX: RP.18, TWE.P$1, U$1.9
TX0: RP.27, TOP.2
TX1: BOTTOM.2, RP.6
TX2: C20.2, ESP32.38
TX3: C21.2, ESP32.9
TX4: RP1.27, TOP1.2
TX5: BOTTOM1.2, RP1.6
TX6: RP2.27, TOP2.2
TX7: BOTTOM2.2, RP2.6
TX8: RP3.27, TOP3.2
TX9: BOTTOM3.2, RP3.6
TX10: RP4.27, TOP4.2
TX11: BOTTOM4.2, RP4.6
USB_DM: J1.D-, R1.2
USB_DM1: J2.D-, U7.1
USB_DM2: J3.D-, R21.2
USB_DM3: J4.D-, R28.2
USB_DM4: J5.D-, R41.2
USB_DM5: J6.D-, R47.2
USB_DM_1: R1.1, RP.46
USB_DM_2: R21.1, RP1.46
USB_DM_3: R28.1, RP2.46
USB_DM_4: R41.1, RP3.46
USB_DM_5: R47.1, RP4.46
USB_DP: J1.D+, R2.2
USB_DP1: J2.D+, U7.12
USB_DP2: J3.D+, R22.2
USB_DP3: J4.D+, R29.2
USB_DP4: J5.D+, R42.2
USB_DP5: J6.D+, R48.2
USB_DP_1: R2.1, RP.47
USB_DP_2: R22.1, RP1.47
USB_DP_3: R29.1, RP2.47
USB_DP_4: R42.1, RP3.47
USB_DP_5: R48.1, RP4.47
USB_VCC: D2.A, J2.VBUS, U7.4
V: C69.+, D7.C, Q2.P2, R35.1, R36.2, R38.2, U11.5
V+: BOTTOM.3, C1.1, D1.C, TOP.3, U2.1, U2.3
V+1: C18.1, C20.3, C21.3, D2.C, U4.1, U4.3
V+2: BOTTOM1.3, C41.1, D3.C, TOP1.3, U8.1, U8.3
V+3: BOTTOM2.3, C57.1, HEATER.1, R35.2, TOP2.3, U9.1, U9.3, U11.4
V+4: BOTTOM3.3, C72.1, D8.C, TOP3.3, U12.1, U12.3
V+5: BOTTOM4.3, C90.1, D9.C, TOP4.3, U14.1, U14.3
VBAT: Q2.P3, U10.3
VDD: C2.1, C3.1, C7.1, C8.1, C9.1, C10.1, C11.1, C14.1, C15.1, C16.2, C17.1, FLASH.8, R7.2, R8.2, R9.2, R10.2, R14.2, RP.1, RP.10, RP.22, RP.26, RP.33, RP.42, RP.43, RP.44, RP.48, RP.49, U1.P2, U1.P14, U2.5, U$1.5
VDD1: C19.1, C22.1, C23.1, C26.1, C30.1, C36.1, C38.1, ESP32.2, MICRO_SD.4, R17.2, U3.1, U3.6, U4.5, U5.1, U5.6, U6.1
VDD2: C39.1, C40.1, C42.1, C43.1, C44.1, C45.1, C46.1, C47.1, C53.1, D4.A, FLASH1.8, GNSS.16, RP1.1, RP1.10, RP1.22, RP1.26, RP1.33, RP1.42, RP1.43, RP1.44, RP1.48, RP1.49, U8.5
VDD3: C55.1, C56.1, C58.1, C59.1, C60.1, C61.1, C62.1, C63.1, FLASH2.8, RP2.1, RP2.10, RP2.22, RP2.26, RP2.33, RP2.42, RP2.43, RP2.44, RP2.48, RP2.49, U9.5
VDD4: C70.1, C71.1, C73.1, C74.1, C75.1, C76.1, C77.1, C78.1, C84.1, C85.1, C87.1, FLASH3.8, FLASH_LOG.8, MICRO_SD1.4, RP3.1, RP3.10, RP3.22, RP3.26, RP3.33, RP3.42, RP3.43, RP3.44, RP3.48, RP3.49, U12.5, U13.2
VDD5: C88.1, C89.1, C91.1, C92.1, C93.1, C94.1, C95.1, C96.1, C102.1, C103.1, C104.1, C105.1, C106.1, FLASH4.8, I2C.1, IC1.3, IC1.28, IC2.2, IC2.6, IC2.8, R55.2, R56.2, R57.2, R58.2, RP4.1, RP4.10, RP4.22, RP4.26, RP4.33, RP4.42, RP4.43, RP4.44, RP4.48, RP4.49, TMP0.1, TMP1.1, U14.5
VPP: D5.C, D6.C, D7.A, Q2.P1, R34.2, U10.4
VSENSE: R38.1, R39.2, RP2.39
VSYNC: CAM.7, ESP32.7
WKUP: R9.1, RP.14, U1.P17
XCLK: CAM.13, ESP32.25
XIN1: C12.1, RP.20, X1.3
XIN2: C51.1, RP1.20, X2.3
XIN3: C67.1, RP2.20, X3.3
XIN4: C82.1, RP3.20, X4.3
XIN5: C100.1, RP4.20, X5.3
XOUT1: R5.2, RP.21
XOUT2: R25.2, RP1.21
XOUT3: R32.2, RP2.21
XOUT4: R45.2, RP3.21
XOUT5: R51.2, RP4.21

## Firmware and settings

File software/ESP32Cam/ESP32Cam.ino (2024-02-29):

// #define V1
#define V2
// #define V3

#if defined V1 || defined V2
#include <SD.h>            // SD Card ESP32
#include <SdFat.h>
#elif defined V3
#define SOC_SDMMC_HOST_SUPPORTED 1
#include <SD_MMC.h>
#endif

#include "esp_camera.h"
#include "Arduino.h"
#include "FS.h"                // SD Card ESP32
#include "soc/soc.h"           // Disable brownour problems
#include "soc/rtc_cntl_reg.h"  // Disable brownour problems
#include "driver/rtc_io.h"
#include "AVIWriter.h"
#include <EEPROM.h>            // read and write from flash memory
#include <SPI.h>
#include <esp_task_wdt.h>
#include <TaskScheduler.h>

#include <UARTBus.hpp>
#include <Indicator.h>
#include <Datatypes.h>

#define NODE 'c'

#define OV5640

#define SPI0_SCK 11
#define SPI0_MOSI 10
#define SPI0_MISO 12
#define SPI0_CS 9
#define SDCARD_MOSI_PIN SPI0_MOSI
#define SDCARD_MISO_PIN SPI0_MISO
#define SDCARD_SS_PIN SPI0_CS
#define SDCARD_SCK_PIN SPI0_SCK

// #define SDMMC_CLK_PIN 11
// #define SDMMC_CMD_PIN 10
// #define SDMMC_D0_PIN 12
// #define SDMMC_D1_PIN 8
// #define SDMMC_D2_PIN 18
// #define SDMMC_D3_PIN 9


#define CAMERA_MODEL_WROVER_KIT // Has PSRAM
#include "camera_pins.h"


/* #define LED_STATUS_PIN 13 */
#if defined V1
#define LED_STATUS_PIN 14
#define LED_ERROR_PIN 19
// #define SWITCH_PIN 0
#define TX0_PIN 2
#define RX0_PIN 20
#define TX1_PIN 16
#define RX1_PIN 17

#elif defined V2 || defined V3
#define LED_STATUS_PIN 13
#define LED_ERROR_PIN 14
#define TX0_PIN 2
#define RX0_PIN 44
#define TX1_PIN 16
#define RX1_PIN 10
#define CAMERA_POWER_PIN 43

#endif

#define MIC_PIN 1

// Constants
#define SERIAL_BAUD 115200
#define BUS_FIFO_SIZE 4096

#define EEPROM_SIZE 5

#define SEND_TLM_FREQ 1

#define CHANGE_FOLDER_FRAMES (30 * 5)


Scheduler scheduler;

void send_tlm();
Task task_send_tlm(
  TASK_SECOND / SEND_TLM_FREQ, TASK_FOREVER,
  &send_tlm, &scheduler, false);



#if defined V1 || defined V2
typedef SdFat32 sd_t;
typedef File32 file_t;
sd_t sd;
#define SPI_CLOCK SD_SCK_MHZ(50)
#define SD_CONFIG SdSpiConfig(SDCARD_SS_PIN, DEDICATED_SPI, SPI_CLOCK)
#elif defined V3
#define sd SD_MMC
#define SD SD_MMC
typedef File file_t;
#endif

AVIWriter avi;


uint8_t framebuffer_static[128 * 1024];
//struct tm lt;


TaskHandle_t thp[2];


uint16_t pictureNumber = 0;
// unsigned frame = 33;

file_t file;

bool camera_ok = false;
bool sd_ok = false;
bool recording = true;

unsigned long start_millis;
unsigned frame_count;
unsigned actual_frame_count;
unsigned wrote_bytes;


UARTBus bus(NODE, Serial2, Serial1);
Indicator indicator(LED_STATUS_PIN, LED_ERROR_PIN);

Shared<FlightMode> flight_mode(FlightMode::STANDBY);

unsigned bus_error_count_;

void setup() {
  // put your setup code here, to run once:

  Serial.begin(115200);

  // delay(5000);

  Serial1.begin(SERIAL_BAUD, SERIAL_8N1, RX0_PIN, TX0_PIN);
  Serial2.begin(SERIAL_BAUD, SERIAL_8N1, RX1_PIN, TX1_PIN);

  bus.begin();
  bus.subscribe(flight_mode, TELEMETRY, 'B', 'm');

  indicator.begin();

  bus_error_count_ = bus.getErrorCount();

#ifdef V2
  pinMode(CAMERA_POWER_PIN, OUTPUT);
  digitalWrite(CAMERA_POWER_PIN, HIGH);
#endif

  EEPROM.begin(EEPROM_SIZE); 

  /* pinMode(SWITCH_PIN, INPUT_PULLUP); */

  camera_config_t config;
  config.ledc_channel = LEDC_CHANNEL_0;
  config.ledc_timer = LEDC_TIMER_0;
  config.pin_d0 = Y2_GPIO_NUM;
  config.pin_d1 = Y3_GPIO_NUM;
  config.pin_d2 = Y4_GPIO_NUM;
  config.pin_d3 = Y5_GPIO_NUM;
  config.pin_d4 = Y6_GPIO_NUM;
  config.pin_d5 = Y7_GPIO_NUM;
  config.pin_d6 = Y8_GPIO_NUM;
  config.pin_d7 = Y9_GPIO_NUM;
  config.pin_xclk = XCLK_GPIO_NUM;
  config.pin_pclk = PCLK_GPIO_NUM;
  config.pin_vsync = VSYNC_GPIO_NUM;
  config.pin_href = HREF_GPIO_NUM;
  config.pin_sscb_sda = SIOD_GPIO_NUM;
  config.pin_sscb_scl = SIOC_GPIO_NUM;
  config.pin_pwdn = PWDN_GPIO_NUM;
  config.pin_reset = RESET_GPIO_NUM;
#ifdef OV5640
  config.xclk_freq_hz = 54000000;
#else
  config.xclk_freq_hz = 28000000;
#endif
  config.pixel_format = PIXFORMAT_JPEG;

  if (psramFound()) {
#ifdef OV5640
    config.frame_size = FRAMESIZE_XGA; // FRAMESIZE_ + QVGA|CIF|VGA|SVGA|XGA|SXGA|UXGA
    avi.video.width = 1024;
    avi.video.height = 768;
    avi.video.fps = 25;
#else
    config.frame_size = FRAMESIZE_SVGA; // FRAMESIZE_ + QVGA|CIF|VGA|SVGA|XGA|SXGA|UXGA
    avi.video.width = 800;
    avi.video.height = 600;
    avi.video.fps = 25;
#endif
    config.jpeg_quality = 12;
    config.fb_count = 8;

  } else {
    config.frame_size = FRAMESIZE_SVGA;
    config.jpeg_quality = 12;
    config.fb_count = 1;
    config.fb_location = CAMERA_FB_IN_DRAM; 
    avi.video.width = 800;
    avi.video.height = 600;
    avi.video.fps = 25;
  }

// Init Camera
  esp_err_t err = esp_camera_init(&config);

  if (err != ESP_OK) {
    Serial.printf("Camera init failed with error 0x%x", err);
    return;
  }
  camera_ok = true;

  #if defined V1 || defined V2

  SPI.begin(SPI0_SCK, SPI0_MISO, SPI0_MOSI, SPI0_CS);

  if (!sd.begin(SD_CONFIG)) {
    Serial.printf("SD Fail");
    sd.initErrorHalt(&Serial);
  }

  #elif defined V3

  Serial.println("SD V2");

  pinMode(SDMMC_CLK_PIN, INPUT_PULLUP);
  pinMode(SDMMC_CMD_PIN, INPUT_PULLUP);

  if (!sd.setPins(SDMMC_CLK_PIN, SDMMC_CMD_PIN, SDMMC_D0_PIN, SDMMC_D1_PIN, SDMMC_D2_PIN, SDMMC_D3_PIN)) {
    Serial.println("Pin Set Fail");
  }

  pinMode(SDMMC_D0_PIN, INPUT_PULLUP);
  pinMode(SDMMC_D1_PIN, INPUT_PULLUP);
  pinMode(SDMMC_D2_PIN, INPUT_PULLUP);
  pinMode(SDMMC_D3_PIN, INPUT_PULLUP);

  while (!sd.begin("/sdcard", true)) {
    Serial.println("SD Fail");
    delay(1000);
  }
  #endif

  uint8_t cardType = SD.cardType();
  if (cardType == CARD_NONE) {
    Serial.println("No SD Card attached");
    // return;
  }
  sd_ok = true;

  if (recording) new_capture();

  Serial.println("Start");

  xTaskCreatePinnedToCore(core0, "core0", 8192, NULL, 10, &thp[0], 0);
  xTaskCreatePinnedToCore(core1, "core1", 8192, NULL, 10, &thp[1], 1);

  task_send_tlm.enable();

  indicator.clearError();
}

void new_capture() {
  EEPROM.get(1, pictureNumber);
  pictureNumber++;

  char file_name[16];
  sprintf(file_name,"/%d.avi", pictureNumber);

  if (!file.open(file_name, O_RDWR | O_CREAT)) {
      Serial.print(" Open failed, ");
  } 
  else {
    Serial.printf("Opened %s\n", file_name);
    //file.write(fb->buf, fb->len); // payload (image), payload lengt
      // file.write(framebuffer_static, fb->len);
      // Serial.printf(" Saved %d kB, ", fb->len / 1000);
    avi.start(file);
  }

  // char dir_name[16];
  // sprintf(dir_name,"/c%d",pictureNumber);
  // if (sd.mkdir(dir_name)) {
  //   Serial.printf("Make dir: %s\n", dir_name);
  // }
  // else {
  //   Serial.printf("Make dir failed: %s\n", dir_name);
  // }

  EEPROM.put(1, pictureNumber);
  EEPROM.commit();

  // captured_millis = millis();
  start_millis = millis();
  frame_count = 0;
  actual_frame_count = 0;
}

void core0(void* argv) {

  for(;;) {
    loop0();
    vTaskDelay(1);
  }
}

void core1(void* argv) {

  for(;;) {
    loop1();
    vTaskDelay(1);
  }
}

void loop() {

}

void loop0() {
  bus.update();

  // Serial1.printf("1");
  // Serial2.printf("2");

  // Serial.printf("core1: %d\n", xPortGetCoreID());

  // Serial.printf(".");

  // Serial.println(analogRead(MIC_PIN));

  bus.sanity(1, camera_ok);
  bus.sanity(2, sd_ok);

  if (bus.getErrorCount() != bus_error_count_) {
    indicator.errorEvent();
    bus_error_count_ = bus.getErrorCount();
  }

  scheduler.execute();
}

void send_tlm() {
  static unsigned last_frame_count;
  static unsigned last_actual_frame_count;
  static unsigned last_wrote_bytes;

  if (camera_ok && sd_ok && recording) {

    unsigned fps = (frame_count - last_frame_count) * SEND_TLM_FREQ;
    unsigned actual_fps = (actual_frame_count - last_actual_frame_count) * SEND_TLM_FREQ;
    unsigned Bps = (wrote_bytes - last_wrote_bytes) * SEND_TLM_FREQ;

    last_frame_count = frame_count;
    last_actual_frame_count = actual_frame_count;
    last_wrote_bytes = wrote_bytes;

    uint8_t buf[BUF_SIZE(4)];
    Packet cam(buf, sizeof(buf));
    cam.set(TELEMETRY, 'c');
    cam.begin()
      .append('C', frame_count)
      .append('F', fps)
      .append('f', actual_fps)
      .append('B', Bps);
    bus.send(cam);

    Serial.printf("%ds: %d (%d) fps, %d kBps, %d %s %d\n", 
      (millis() - start_millis) / 1000, fps, actual_fps, Bps / 1000,
      bus_error_count_, bus.error_code_, flight_mode.value());

    indicator.blink(500);
  }
  else indicator.blink(10);
}

void loop1() {

  // Serial.printf("core0: %d\n", xPortGetCoreID());

  /* if (!digitalRead(SWITCH_PIN)) recording = true; */

  // unsigned long start_millis = millis();

  if (flight_mode.value() == FlightMode::RECOVERY) {
    recording = false;
#ifdef V2
    digitalWrite(CAMERA_POWER_PIN, LOW);
#endif
  }
  else {
    if (!recording) {
        recording = true;
#ifdef V2
        digitalWrite(CAMERA_POWER_PIN, HIGH);
#endif
        new_capture();
      }
  }

  if (camera_ok && sd_ok && recording) {
    camera_fb_t * fb = NULL;
    // Take Picture with Camera
    fb = esp_camera_fb_get();
    if (!fb) {
      Serial.println("Camera capture failed");
      return;
    }
    // memcpy(framebuffer_static, fb->buf, fb->len);

  // unsigned frame_millis = millis() - captured_millis;
  // captured_millis += 1000.0f / avi.video.fps

// Path where new picture will be saved in SD Card
    // String path = "/c" + String(pictureNumber) + "/pic" + String(i) + ".jpg";

    // fs::FS &fs = SD;
    // Serial.print(path);

#if defined V1 || defined V2
    // unsigned long makefile_millis = millis();

    avi.addVideoFrame(fb->buf, fb->len);
    // avi.updateParameters();

    // if (!file.open(path.c_str(), O_RDWR | O_CREAT)) {
    //   Serial.print(" Open failed, ");
    // } else {
    //   //file.write(fb->buf, fb->len); // payload (image), payload lengt
    //   makefile_millis = millis();
    //   file.write(framebuffer_static, fb->len);
      // Serial.printf("%d kB, ", fb->len / 1000);
    // }
    // file.close();
#elif defined V3
    File file = SD_MMC.open(path.c_str(), FILE_WRITE);
    if (!file) {
      Serial.print(" Open failed, ");
    }else {
      //file.write(fb->buf, fb->len); // payload (image), payload lengt
      file.write(framebuffer_static, fb->len);
      // Serial.printf(" Saved %d kB, ", fb->len / 1000);
    }
    file.close();
#endif

    esp_camera_fb_return(fb);

    frame_count++;
    actual_frame_count++;

    float frame_per_ms = avi.video.fps / 1000.0;
    float frame_ms = 1000.0 / avi.video.fps;

    // Serial.printf("%d %f %f\n", millis() - start_millis, frame_count / frame_per_ms, frame_ms);

    while (millis() - start_millis > (unsigned)(frame_count / frame_per_ms + frame_ms)) {
      frame_count++;
      avi.skipFrame();
      // Serial.print("skip ");
    }
    while (millis() - start_millis < (unsigned)(frame_count / frame_per_ms - frame_ms)) {
      delay(1);
    }

    wrote_bytes += fb->len;

    // unsigned long captured_millis = millis();

    // frame_count++;
    // i++;
    // unsigned long end_millis = millis();

    // unsigned long m = end_millis - start_millis;

    // long sleep_millis = frame - m;

    // if (m > frame) { // skip frame
    //   // avi.skipFrame();
    //   sleep_millis = sleep_millis % frame;
    //   i++;
    // }

    // Serial.printf("%ld cap, %ld write, %ld sleep, skip:%d\n",
    //               captured_millis - start_millis,
    //               // makefile_millis - captured_millis,
    //               end_millis - captured_millis,
    //               sleep_millis, m > frame);

    // delay(sleep_millis);

    // indicator.blink(1);
  }
}

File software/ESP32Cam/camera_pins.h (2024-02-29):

#if defined(CAMERA_MODEL_WROVER_KIT)

#define PWDN_GPIO_NUM    -1
#define RESET_GPIO_NUM   -1
#define XCLK_GPIO_NUM    48
#define SIOD_GPIO_NUM    5
#define SIOC_GPIO_NUM    4

#define Y9_GPIO_NUM      47
#define Y8_GPIO_NUM      45
#define Y7_GPIO_NUM      46
#define Y6_GPIO_NUM      38
#define Y5_GPIO_NUM      40
#define Y4_GPIO_NUM      42
#define Y3_GPIO_NUM      41
#define Y2_GPIO_NUM      39
#define VSYNC_GPIO_NUM   7
#define HREF_GPIO_NUM    15
#define PCLK_GPIO_NUM    3

#elif defined(CAMERA_MODEL_ESP_EYE)
#define PWDN_GPIO_NUM    -1
#define RESET_GPIO_NUM   -1
#define XCLK_GPIO_NUM    4
#define SIOD_GPIO_NUM    18
#define SIOC_GPIO_NUM    23

#define Y9_GPIO_NUM      36
#define Y8_GPIO_NUM      37
#define Y7_GPIO_NUM      38
#define Y6_GPIO_NUM      39
#define Y5_GPIO_NUM      35
#define Y4_GPIO_NUM      14
#define Y3_GPIO_NUM      13
#define Y2_GPIO_NUM      34
#define VSYNC_GPIO_NUM   5
#define HREF_GPIO_NUM    27
#define PCLK_GPIO_NUM    25

#elif defined(CAMERA_MODEL_M5STACK_PSRAM)
#define PWDN_GPIO_NUM     -1
#define RESET_GPIO_NUM    15
#define XCLK_GPIO_NUM     27
#define SIOD_GPIO_NUM     25
#define SIOC_GPIO_NUM     23

#define Y9_GPIO_NUM       19
#define Y8_GPIO_NUM       36
#define Y7_GPIO_NUM       18
#define Y6_GPIO_NUM       39
#define Y5_GPIO_NUM        5
#define Y4_GPIO_NUM       34
#define Y3_GPIO_NUM       35
#define Y2_GPIO_NUM       32
#define VSYNC_GPIO_NUM    22
#define HREF_GPIO_NUM     26
#define PCLK_GPIO_NUM     21

#elif defined(CAMERA_MODEL_M5STACK_V2_PSRAM)
#define PWDN_GPIO_NUM     -1
#define RESET_GPIO_NUM    15
#define XCLK_GPIO_NUM     27
#define SIOD_GPIO_NUM     22
#define SIOC_GPIO_NUM     23

#define Y9_GPIO_NUM       19
#define Y8_GPIO_NUM       36
#define Y7_GPIO_NUM       18
#define Y6_GPIO_NUM       39
#define Y5_GPIO_NUM        5
#define Y4_GPIO_NUM       34
#define Y3_GPIO_NUM       35
#define Y2_GPIO_NUM       32
#define VSYNC_GPIO_NUM    25
#define HREF_GPIO_NUM     26
#define PCLK_GPIO_NUM     21

#elif defined(CAMERA_MODEL_M5STACK_WIDE)
#define PWDN_GPIO_NUM     -1
#define RESET_GPIO_NUM    15
#define XCLK_GPIO_NUM     27
#define SIOD_GPIO_NUM     22
#define SIOC_GPIO_NUM     23

#define Y9_GPIO_NUM       19
#define Y8_GPIO_NUM       36
#define Y7_GPIO_NUM       18
#define Y6_GPIO_NUM       39
#define Y5_GPIO_NUM        5
#define Y4_GPIO_NUM       34
#define Y3_GPIO_NUM       35
#define Y2_GPIO_NUM       32
#define VSYNC_GPIO_NUM    25
#define HREF_GPIO_NUM     26
#define PCLK_GPIO_NUM     21

#elif defined(CAMERA_MODEL_M5STACK_ESP32CAM)
#define PWDN_GPIO_NUM     -1
#define RESET_GPIO_NUM    15
#define XCLK_GPIO_NUM     27
#define SIOD_GPIO_NUM     25
#define SIOC_GPIO_NUM     23

#define Y9_GPIO_NUM       19
#define Y8_GPIO_NUM       36
#define Y7_GPIO_NUM       18
#define Y6_GPIO_NUM       39
#define Y5_GPIO_NUM        5
#define Y4_GPIO_NUM       34
#define Y3_GPIO_NUM       35
#define Y2_GPIO_NUM       17
#define VSYNC_GPIO_NUM    22
#define HREF_GPIO_NUM     26
#define PCLK_GPIO_NUM     21

#elif defined(CAMERA_MODEL_M5STACK_UNITCAM)
#define PWDN_GPIO_NUM     -1
#define RESET_GPIO_NUM    15
#define XCLK_GPIO_NUM     27
#define SIOD_GPIO_NUM     25
#define SIOC_GPIO_NUM     23

#define Y9_GPIO_NUM       19
#define Y8_GPIO_NUM       36
#define Y7_GPIO_NUM       18
#define Y6_GPIO_NUM       39
#define Y5_GPIO_NUM        5
#define Y4_GPIO_NUM       34
#define Y3_GPIO_NUM       35
#define Y2_GPIO_NUM       32
#define VSYNC_GPIO_NUM    22
#define HREF_GPIO_NUM     26
#define PCLK_GPIO_NUM     21

#elif defined(CAMERA_MODEL_AI_THINKER)
#define PWDN_GPIO_NUM     32
#define RESET_GPIO_NUM    -1
#define XCLK_GPIO_NUM      0
#define SIOD_GPIO_NUM     26
#define SIOC_GPIO_NUM     27

#define Y9_GPIO_NUM       35
#define Y8_GPIO_NUM       34
#define Y7_GPIO_NUM       39
#define Y6_GPIO_NUM       36
#define Y5_GPIO_NUM       21
#define Y4_GPIO_NUM       19
#define Y3_GPIO_NUM       18
#define Y2_GPIO_NUM        5
#define VSYNC_GPIO_NUM    25
#define HREF_GPIO_NUM     23
#define PCLK_GPIO_NUM     22

#elif defined(CAMERA_MODEL_TTGO_T_JOURNAL)
#define PWDN_GPIO_NUM      0
#define RESET_GPIO_NUM    15
#define XCLK_GPIO_NUM     27
#define SIOD_GPIO_NUM     25
#define SIOC_GPIO_NUM     23

#define Y9_GPIO_NUM       19
#define Y8_GPIO_NUM       36
#define Y7_GPIO_NUM       18
#define Y6_GPIO_NUM       39
#define Y5_GPIO_NUM        5
#define Y4_GPIO_NUM       34
#define Y3_GPIO_NUM       35
#define Y2_GPIO_NUM       17
#define VSYNC_GPIO_NUM    22
#define HREF_GPIO_NUM     26
#define PCLK_GPIO_NUM     21

#else
#error "Camera model not selected"
#endif

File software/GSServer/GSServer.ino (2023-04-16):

#define CONFIG_ASYNC_TCP_USE_WDT 0

#include <TinyGPS++.h>
#include <WiFi.h>
#include <esp_task_wdt.h>
#include <ESPmDNS.h>
#include <ESPAsyncWebServer.h>
#include <AsyncJson.h>
#include <SPIFFS.h>
#include <CAN.h>
#include "command.hpp"
#include "LCD.h"

#define AP_MODE

#define GPS_RX_PIN 5
#define GPS_TX_PIN 18
#define CAN_RX_PIN 32
#define CAN_TX_PIN 33
#define LED_PIN 2
#define SWITCH_PIN_1 12
#define SWITCH_PIN_2 13
#define SWITCH_PIN_3 14

#define CAN_BAUD 125000
static const uint32_t GPSBaud = 9600;

#define RETURN_COMMAND_MAX 100
#define SEND_COMMAND_FREQ 1
#define BLINK_MS 50

#define GPS_SWITCH_FREQ 0.1

const char ssid[] = "Rockoon-GS1";
const char pass[] = "rockoon-gs1";
/* const char ssid[] = "Rockoon-GS2"; */
/* const char pass[] = "rockoon-gs2"; */
const IPAddress ip(192,168,1,1);
const IPAddress subnet(255,255,255,0);
AsyncWebServer server(80);

TaskHandle_t thp[1];

LCD lcd;
TinyGPSPlus gps;
HardwareSerial ss(2);

CANChannel can_channel;
HexChannel hex_channel;

Command* received_buf;
unsigned received_buf_size;
unsigned received_pointer;

/* Command* received_remote_commands; */
/* uint32_t received_remote_count; */
/* uint32_t received_remote_max; */

/* Command* received_local_commands; */
/* uint32_t received_local_count; */
/* uint32_t received_local_max; */

enum class SwitchState {
  NotSelected,
  NoLaunch,
  AllowLaunch,
};

SwitchState switch_state = SwitchState::NotSelected;
unsigned long blink_ms;
unsigned long sent_command_ms;

float rocket_lat;
float rocket_lng;
uint32_t rocket_gps_received;


void setup() {
  Serial.begin(115200);
  ss.begin(GPSBaud, SERIAL_8N1, GPS_RX_PIN, GPS_TX_PIN);
  Wire.begin(21, 22);

  /* pinMode(21, INPUT_PULLUP); */
  /* pinMode(22, INPUT_PULLUP); */

  pinMode(LED_PIN, OUTPUT);
  pinMode(SWITCH_PIN_1, INPUT_PULLUP);
  pinMode(SWITCH_PIN_2, INPUT_PULLUP);
  pinMode(SWITCH_PIN_3, INPUT_PULLUP);

  digitalWrite(LED_PIN, HIGH);

  i2c_scanner();

  lcd.begin();

  init_datastore();

  delay(1000);

  init_server();


  xTaskCreatePinnedToCore(loop_task, "core0", 8192, NULL, 3, &thp[0], 0);

  delay(1000);

  CAN.setPins(CAN_RX_PIN, CAN_TX_PIN);
  CAN.begin(CAN_BAUD * 2);
  /* CAN.onReceive(onCANReceive); */


  digitalWrite(LED_PIN, LOW);

  char line1[] = "GPS Unavailable ";
  char line2[] = "----------------";

  strncpy(lcd.line1, line1, 16);
  strncpy(lcd.line2, line2, 16);
  lcd.show();
}

void loop() {
  
}

void loop_task(void *args) {
  for(;;) {
    esp_task_wdt_reset();
    loop1();
  }
}

void loop1() {
  int packetSize = CAN.parsePacket();
  if (packetSize > 0) onCANReceive(packetSize);



  // Read GPS
  while(ss.available()){
    char c = ss.read();
    gps.encode(c);
  }

  // Update location
  if (!gps.location.isValid()) {

  }
  else if (gps.location.isUpdated()) {
    /* struct tm t; */
    /* t.tm_year  = gps.date.year() - 1900; */
    /* t.tm_mon   = gps.date.month() - 1; */
    /* t.tm_mday  = gps.date.day(); */
    /* t.tm_hour  = gps.time.hour(); */
    /* t.tm_min   = gps.time.minute(); */
    /* t.tm_sec   = gps.time.second(); */
    /* t.tm_isdst = -1; */
    /* time_t epoch = mktime(&t); */

    Command position('P', 0, 0, 4);
    position.entries[0].set('O', (float)gps.location.lng());
    position.entries[1].set('A', (float)gps.location.lat());
    position.entries[2].set('H', (float)gps.altitude.meters());
    position.entries[3].set('D', (uint32_t)gps.date.value());
    position.entries[3].set('T', (uint32_t)gps.time.value());

    can_channel.tx.push(position);
    sendCAN();

    addReceivedCommand(position);
  }

  int step = int(millis() * GPS_SWITCH_FREQ) % 1000;
  if (step < 500 && step % 10 == 0) {
    strcpy(lcd.line1, "GS      ");
    if (gps.location.age() >= 100000) {
      snprintf(lcd.line2, 7, "N/A  ");
    }
    else {
      snprintf(lcd.line2, 7, "%3.1fs ", (gps.location.age() / 1000.0));
    }
    printDegree(lcd.line1 + 7, gps.location.lng());
    printDegree(lcd.line2 + 7, gps.location.lat());
    /* snprintf(lcd.line1 + 6, 11, "%3.7f", gps.location.lng()); */
    /* snprintf(lcd.line2 + 6, 11, "%3.7f", gps.location.lat()); */
    lcd.show();
  }
  else if (step >= 500 && step % 10 == 0) {
    strcpy(lcd.line1, "Rocket  ");
    if (millis() - rocket_gps_received >= 100000) {
      snprintf(lcd.line2, 9, "N/A     ");
    }
    else {
      snprintf(lcd.line2, 9, "%3.1fs   ",
               (millis() - rocket_gps_received) / 1000.0);
    }
    printDegree(lcd.line1 + 7, rocket_lng);
    printDegree(lcd.line2 + 7, rocket_lat);
    /* snprintf(lcd.line1 + 6, 11, "%3.7f", rocket_lng); */
    /* snprintf(lcd.line2 + 6, 11, "%3.7f", rocket_lat); */
    lcd.show();
  }

  lcd.update();

  /* server.handleClient(); */

  /* Serial.print("data: "); */
  /* Serial.println(received_count); */

  /* delay(50); */

  /* addDummyCANData(); */

  if (millis() - blink_ms >= BLINK_MS) {
    digitalWrite(LED_PIN, LOW);
  }

  if      (!digitalRead(SWITCH_PIN_2))
    switch_state = SwitchState::NotSelected;
  else if (!digitalRead(SWITCH_PIN_1))
    switch_state = SwitchState::NoLaunch;
  else if (!digitalRead(SWITCH_PIN_3))
    switch_state = SwitchState::AllowLaunch;
  else
    switch_state = SwitchState::NotSelected;

  // Send mode command
  if (millis() > sent_command_ms + 1000 / SEND_COMMAND_FREQ) {
    printSwitchState();

    if (switch_state != SwitchState::NotSelected) {
      Command command('m', 'L', 0, 1);
      uint8_t type = switch_state == SwitchState::AllowLaunch ? 'F' : 'S';
      command.entries[0].set(type);

      can_channel.tx.push(command);
      sendCAN();
      addReceivedCommand(command);
    }
    sent_command_ms = millis();
  }
}

void printDegree(char* buf, float deg) {
  int d = (int)deg;
  int m = (int)((deg - d) * 60);
  int s = (int)(((deg - d) * 60 - m) * 60);
  sprintf(buf, "%3d'%02d'%02d", (int)d, (int)m, (int)s);
}


void onCANReceive(int packetSize) {
  if (CAN.packetRtr()) return;

  /* Serial.print("CAN Core: "); */
  /* Serial.println(xPortGetCoreID()); */

  uint8_t id = CAN.packetId();
  uint8_t len = CAN.packetDlc();

  /* Serial.print("CAN R  "); */
  /* Serial.print(id); */
  /* Serial.print(" "); */
  /* Serial.print(len); */
  /* Serial.print(": "); */

  uint8_t data[8];

  for (int n = 0; n < len; n++) {
    data[n] = CAN.read();
    /* Serial.print(data[n], HEX); */
  }

  /* Serial.println(); */

  if (can_channel.receive(id, data, len)) {
    addReceivedCommand(can_channel.rx);

    if (can_channel.rx.id == 'L') {
      union Payload p;
      if (can_channel.rx.get('A', 0, p)) {
        rocket_lat = p.int_ / 10000000.0;
        rocket_gps_received = millis();
      }
      if (can_channel.rx.get('O', 0, p)) {
        rocket_lng = p.int_ / 10000000.0;
        rocket_gps_received = millis();
      }
    }
  }
}
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

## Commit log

2022-12-02 communicationの回路図と基盤の途中経過です。Lo-Raの部分が終わって、残りはTweLiteをやれば完成のはずです。初めて基盤の設計をしているので不備が必ずあると思います。確認お願いします。
    [communication.brd, communication.sch]
2022-12-08 communicationの層が一応完成しました。確認お願いします
    [communication.brd, communication.sch]
2022-12-08 Revert "communicationの層が一応完成しました。確認お願いします"
    This reverts commit c7c23561daafb7c0ad8373af90d18b3355d51587.
    [communication.brd, communication.sch]
2022-12-15 communication 回路図、基盤 更新
    [communication.brd, communication.sch]
2022-12-15 communication基盤一部改良、GNSS基盤
    [communication.brd, gnss.brd]
2022-12-15 変更点: communication_LoRaをUART接続に変換 gnss_GPSのRTX接続およびRESETの追加
    [communication.brd, communication.sch, gnss.brd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]
2022-12-21 loggerの基盤終わりました！
    [logger.brd]
2022-12-30 センサーの基盤完了しました。エラー処理とか諸々終わってないので年末年始で頑張ります。抵抗値とかなにも入力してなかったのでしばらくかかりそうです。
    [sensor.brd, sensor.sch]
2023-01-16 べたGND前です。esp32のschはノータッチなのでここに上がってないです。よろしくお願いします。
    [communication.brd, communication.sch, esp32cam.brd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]
2023-01-16 LiPoのだけできなかったのですが、それ以外のべたGND済のものです。
    [communication.brd, esp32cam.brd, gnss.brd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]
2023-01-16 LoRa ResetとTWELITE TX&RXの引き出しピンを追加
    [communication.brd, communication.sch]
2023-01-16 シルクを調整
    [communication.brd, communication.sch, esp32cam.brd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]
2023-01-16 esp32cam途中
    [esp32cam.brd, esp32cam.sch]
2023-01-17 変更点:カメラモジュール・SDカード・LED1,2接続、未接続だったVDD、GNDの接続 一応完成したはずです。確認お願いします。
    [esp32cam.brd, esp32cam.sch]
2023-01-17 若干修正
    [esp32cam.brd, esp32cam.sch, lipo.brd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]
2023-01-17 ステンシルを追加
    [stencil.brd]
2023-02-04 Update README.md
    詳細設定書き込みたいのでテストです
2023-02-04 Update README.md
    詳細設定自分なりに考えてみました。評価お願いします。
2023-02-12 プログラムの雛形を追加
2023-02-14 SDカード書き込みテスト
2023-02-18 I2Cテスト
2023-02-23 共通部分（バス，LED）
2023-02-25 ログ書き込み，バス通信
2023-02-26 TWELITE通信
2023-02-26 カメラコードの追加です。
2023-02-26 センサー完成
2023-02-26 バス不具合修正
2023-02-26 ロゴを追加
2023-02-27 連番画像から動画を作成するスクリプトを追加
2023-02-28 地上局を追加
2023-02-28 delay追加
2023-03-03 起動時から動作するように&SDのフォルダ内にファイルが増えすぎると遅くなるので1分ごとに分けるようにした
2023-03-03 バス処理とメイン処理を並列化
2023-03-03 SDのログの読み込み
2023-03-03 地上局からのテレメを非表示に
2023-03-03 並列化は無しで
2023-03-03 緯度経度のデコードを追加
2023-03-03 GPS座標のプロット
2023-03-03 GPS座標のプロット（修正）
2023-03-04 CSV出力を追加
2023-04-05 テレメトリ画面を追加
2023-04-09 パケットの表示を実装
2023-04-09 パケットを送信元別に表示
2023-04-09 図を追加
2023-04-10 図の描画範囲を変更可能に
2023-04-11 再生コントロールを追加
2023-04-12 地図を追加
2023-04-15 動画再生を実装
2023-04-15 警告表示を追加
2023-04-16 develop最新
2023-04-16 Actions設定
2023-04-16 ビルド先を相対パスに
2023-04-22 画像を追加
2023-04-22 ルーターを修正
2023-04-22 404リダイレクトを追加
2023-05-07 LiPo回路修正，新LoRa
    [communication.brd, communication.sch, lipo.brd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]
2023-05-07 アナログ入力を修正
    [lipo.brd, lipo.sch]
2023-05-23 ブランチテスト(ほとんど変更していません)
    [communication.brd]
2023-05-24 issue#5:TELES/communication 基盤設計完了したので確認お願いします。
    [communication.brd]
2023-05-24 communication_修正
    [communication.brd]
2023-05-25 LiPoモジュールの基板設計です。
    [lipo.brd]
2023-05-27 回路微修正
    [communication.brd, esp32cam.brd, esp32cam.sch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]
2023-05-27 ベタ・シルク調整
    [communication.brd, communication.sch, esp32cam.brd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]
